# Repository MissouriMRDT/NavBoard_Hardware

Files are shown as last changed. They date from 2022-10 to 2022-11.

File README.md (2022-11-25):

# MRDT NavBoard Hardware
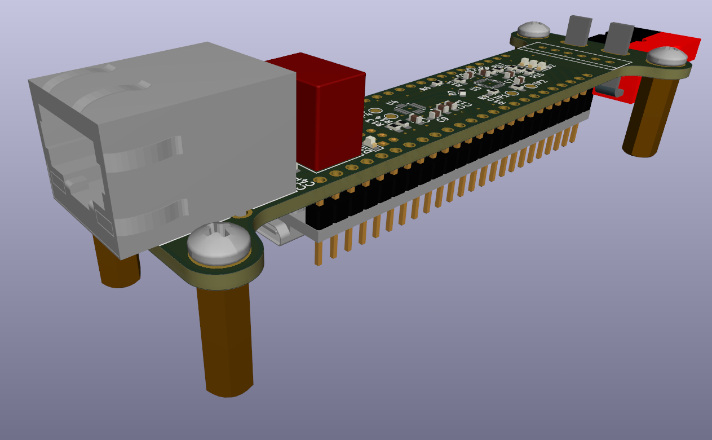
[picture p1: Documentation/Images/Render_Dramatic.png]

## Purpose
The Navigation (Nav) Board is responsible for containing, supplying, and interfacing the equipment required to determine the rover's position and orientation. This board does this by utilizing 2 inertial measurement units (IMUs) and a connection to an external GPS receiver. This data is processed and sent to the rest of the rover via an ethernet connection.
## Design
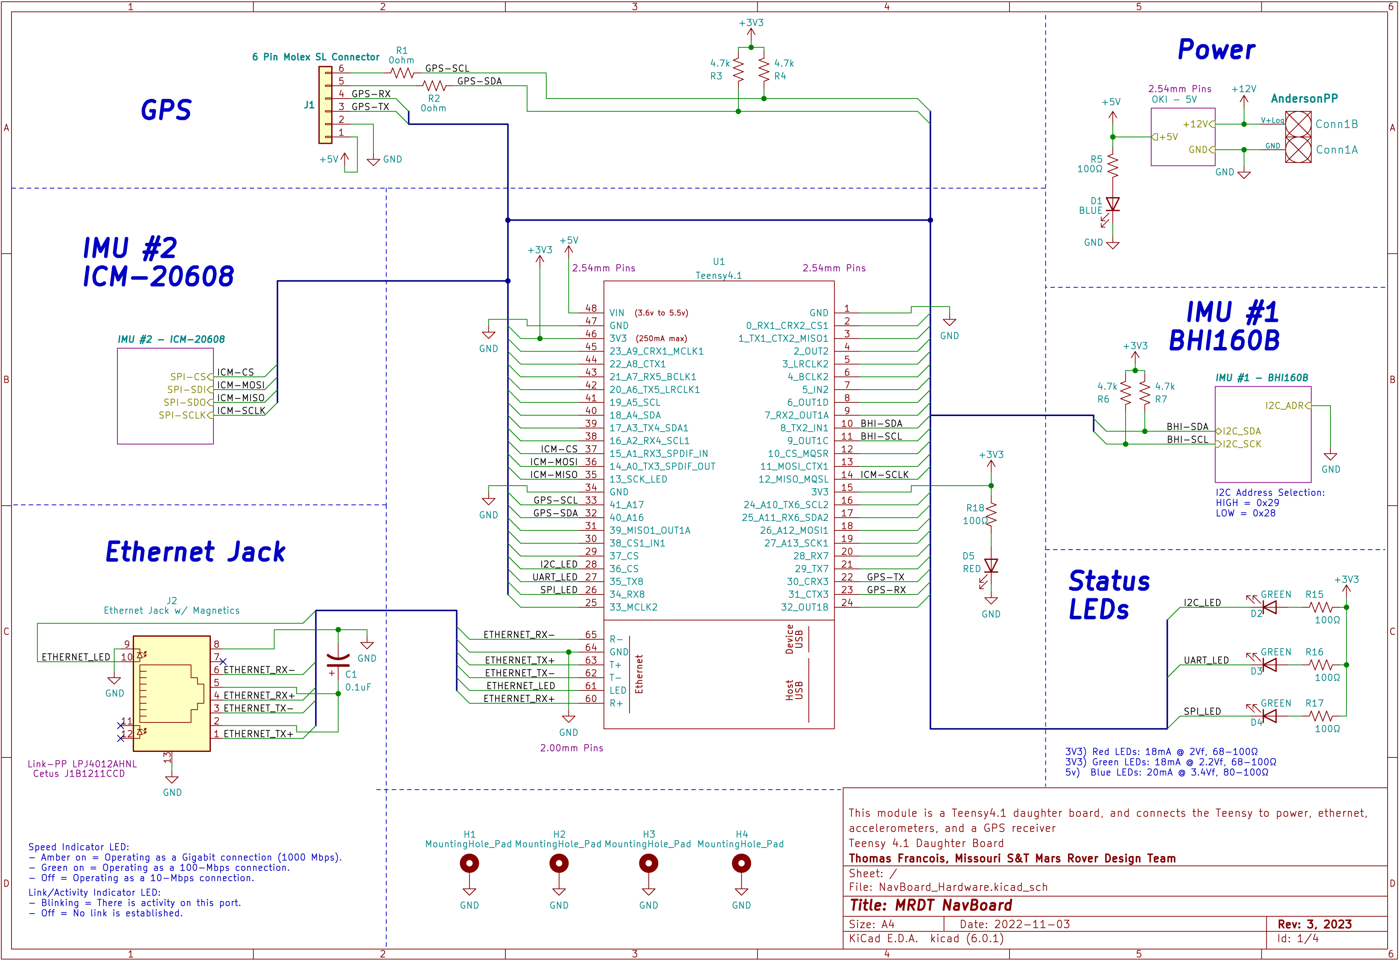
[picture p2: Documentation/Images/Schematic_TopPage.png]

This revision of the board is a new design, based on the components and connections from the 2022/2023 Rev 2 designs. The goal of this design was to make the board as small as possible, and to mount onto a Teensy 4.1 instead of a raspberry pi.

This design utilizes a 4-layer PCB with holes for M3 mounting screws on 15mm standoffs. The Teensy is soldered onto one side of the board, and all of the smd components are mounted on the other side.

This design also includes an ethernet RJ45 jack for allowing ethernet connectivity to the Teensy.

## Required External Connections
 - +12V
 - GPS (I2C and UART)
 - Teensy 4.1
 - Ethernet

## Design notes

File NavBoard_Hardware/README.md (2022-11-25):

# MRDT NavBoard PCB
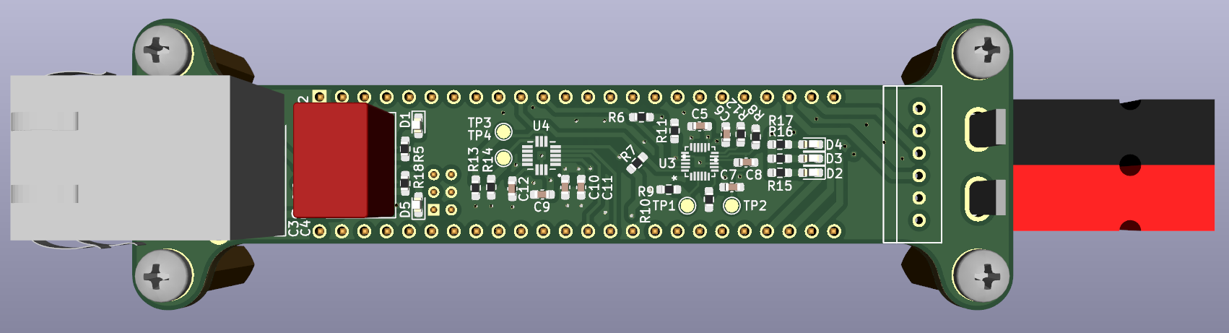
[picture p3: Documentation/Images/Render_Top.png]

## Dimensions
 - 100mm Long (124.29mm w/ Horizontal Power Poles)
 - 33.1mm Wide
## Board Specifications
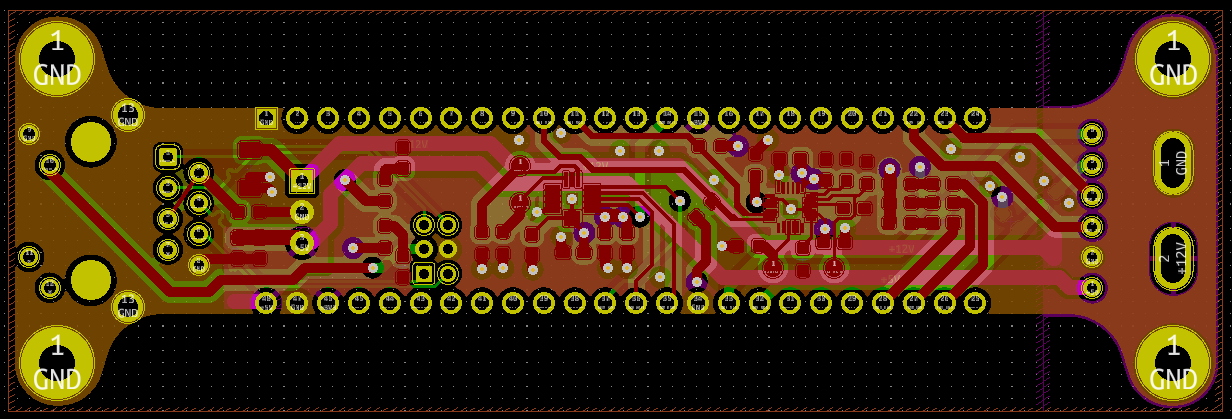
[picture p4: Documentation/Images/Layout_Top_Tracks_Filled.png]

 - 4-layer
  -- Top Copper (Signals, SMD Components, Ground Pour)
  -- Ground Copper
  -- Power Copper (3V3, 5V, 12V)
  -- Bottom Copper (Signals, Ethernet, Ground Pour)
 - 1-oz Copper
 - 1.6mm Thick
## Mounting Points
This module is designed as a daughter board to be mounted on top of a Teensy 4.1 microcontroller. There are holes at each corner of the board for mounting M3 standoffs. These holes are electrically connected to ground.

The powerpole connectors can be mounted vertically to reduce horizontal space.

The Teensy 4.1 needs to be mounted with the USB port facing the Ethernet port.

The Teensy 4.1 also needs to be mounted so that its reset button is accessible.

The MicroSD card should be accessible if the PowerPole connectors do not extend below the holes too much.

The Teensy 4.1 ethernet pins are 2.00mm pitch, NOT the standard 2.54mm. These also will likely need to be longer than standard 2.00mm pins, as 2.00 pins are shorter in length an 2.54mm pins.

The Teensy 4.1 CAN be socketed onto the PCB, but it is recommended for structural integrity reasons that it be direcly soldered into place using 2.54mm and 2.00mm pins.

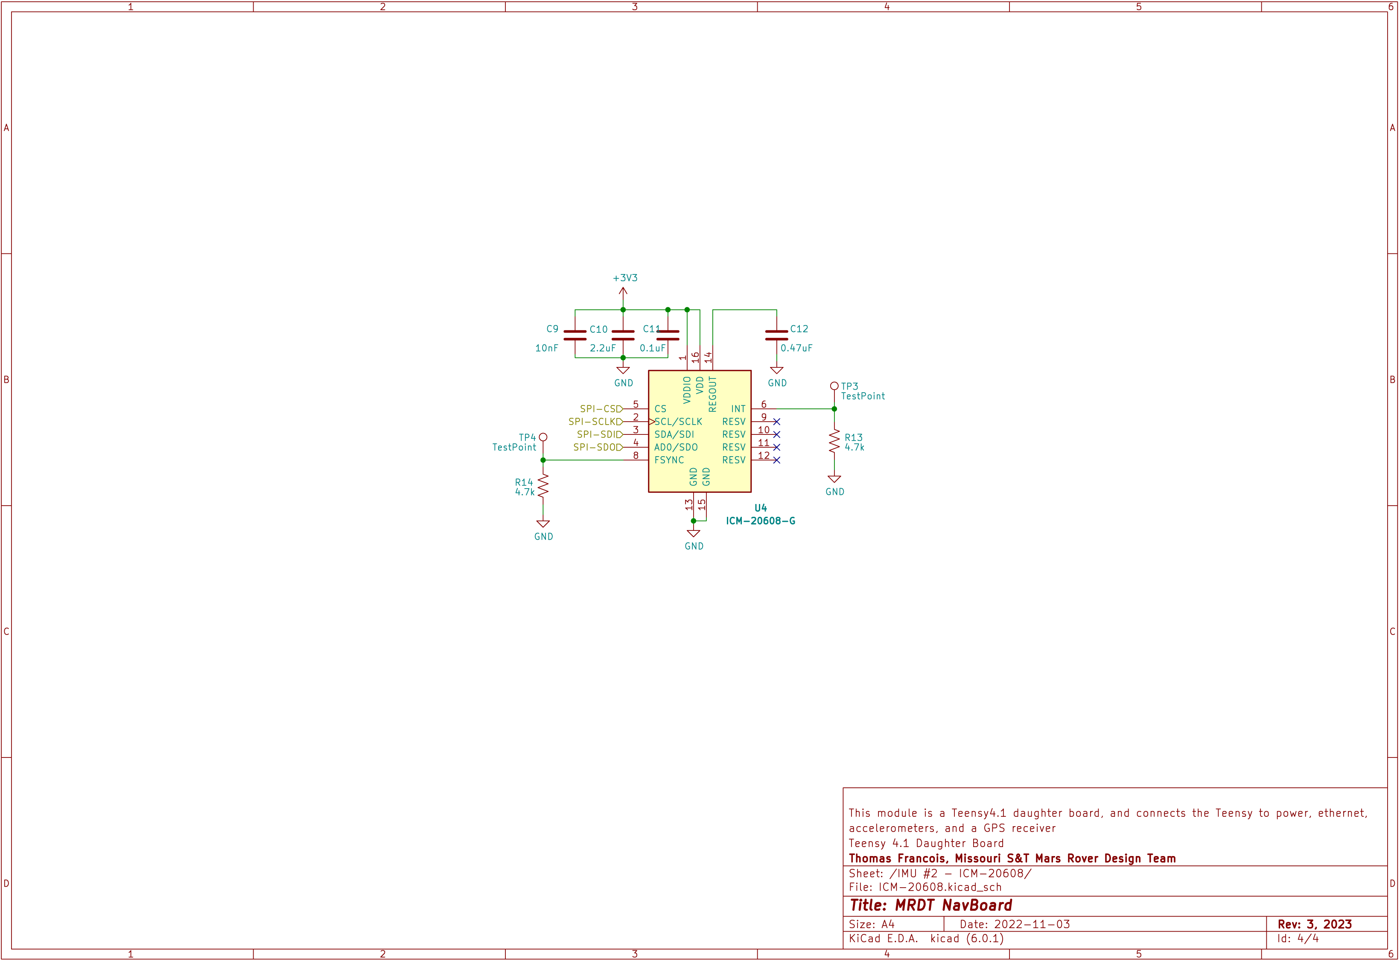
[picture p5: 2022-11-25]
Documentation/Images/Schematic_ICM-20608.png

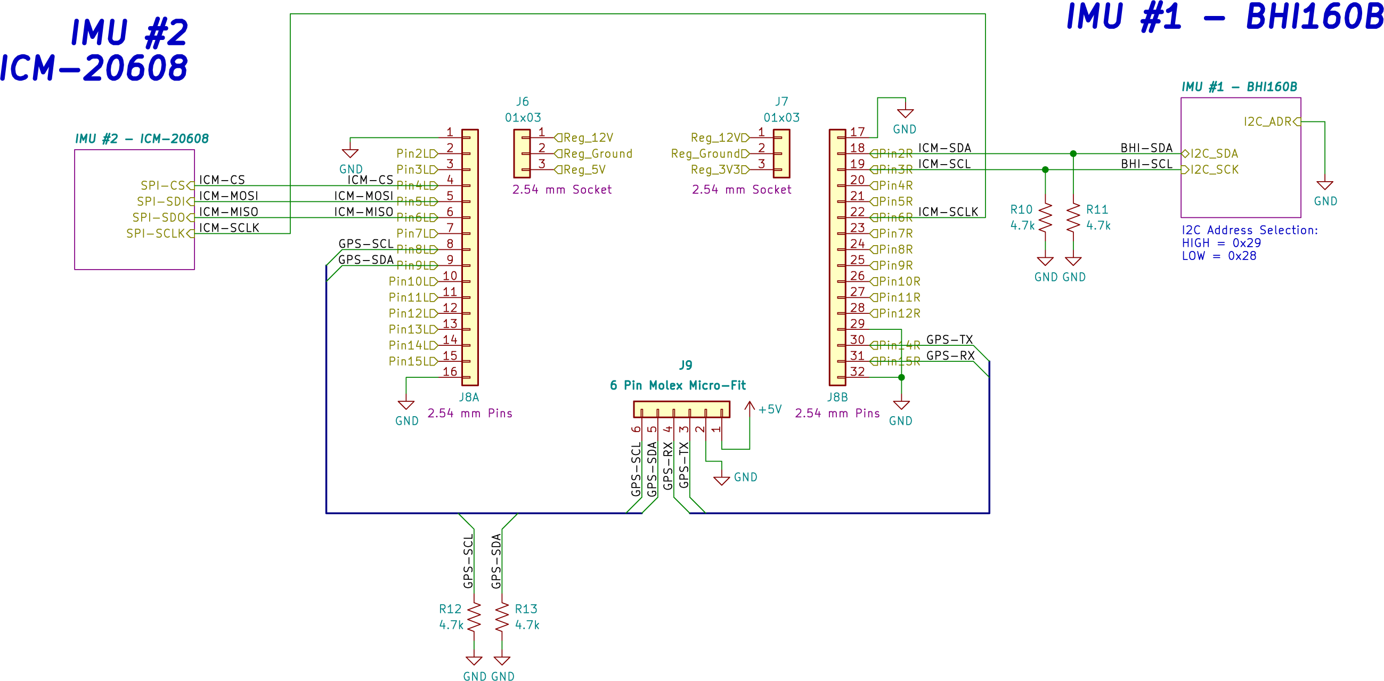
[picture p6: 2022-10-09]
Documentation/Schematic Screenshots/Top Board Sheet.png

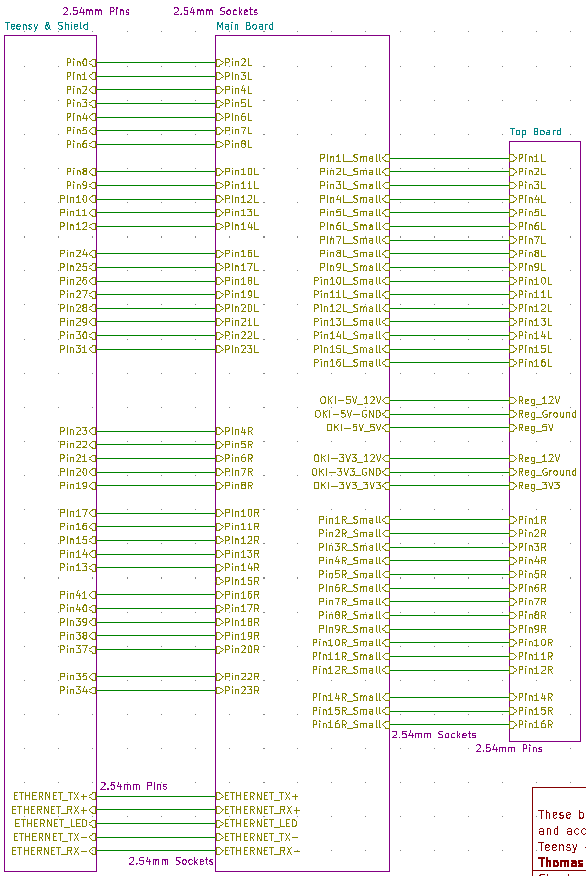
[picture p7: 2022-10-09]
Documentation/Schematic Screenshots/Screenshot 2022-10-09 160128.png

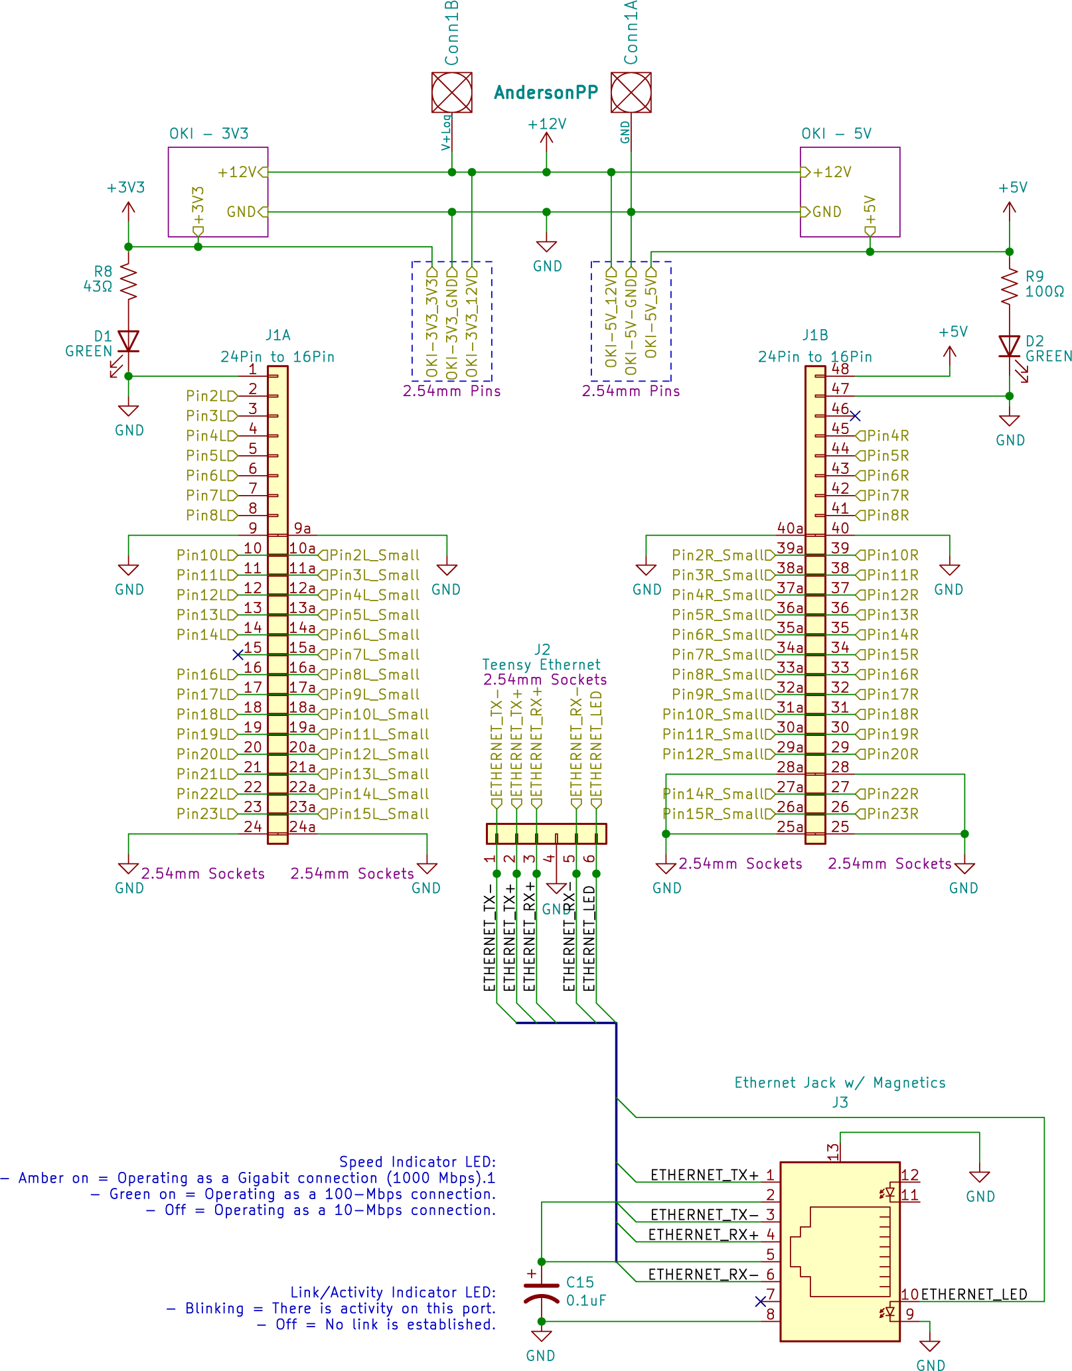
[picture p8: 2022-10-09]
Documentation/Schematic Screenshots/Main Board Sheet.png

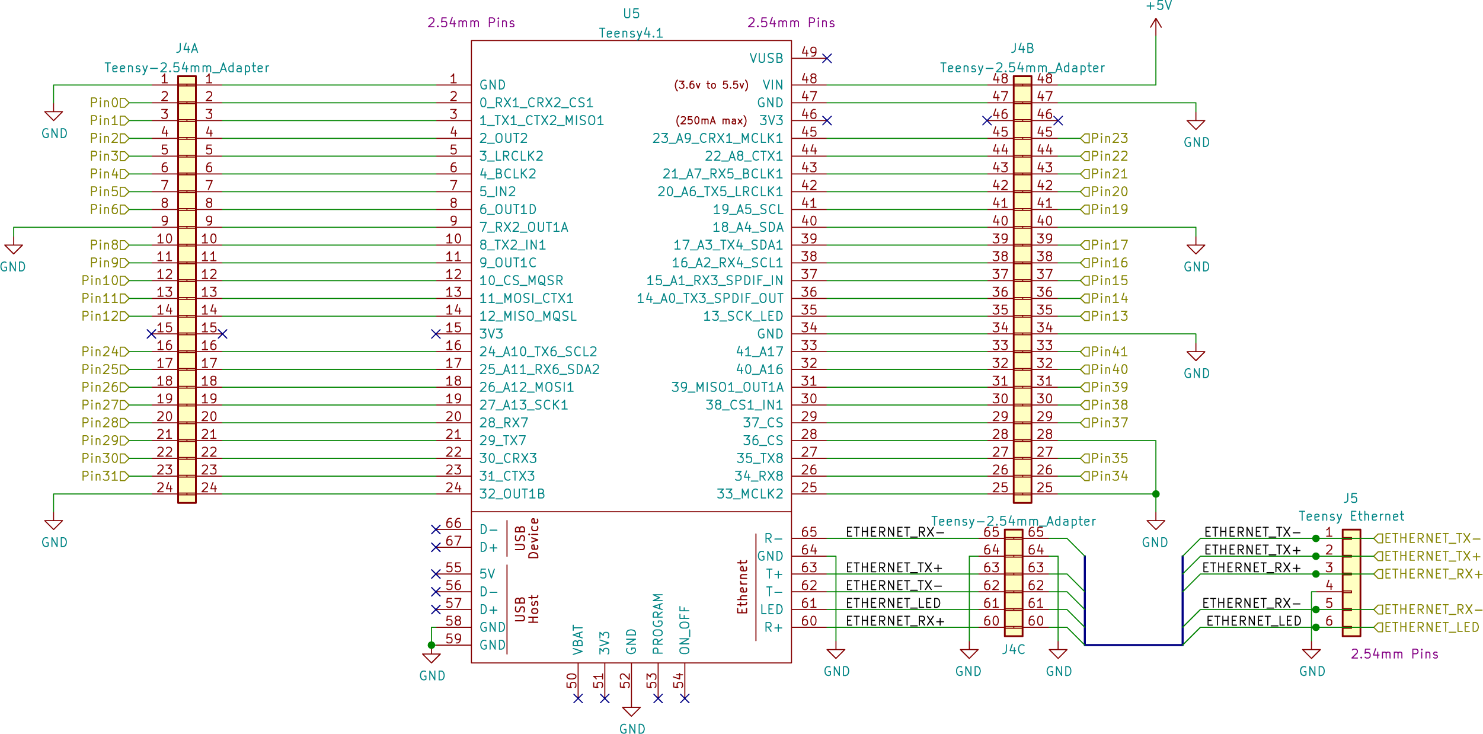
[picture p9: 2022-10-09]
Documentation/Schematic Screenshots/Teensy Shield Sheet.png

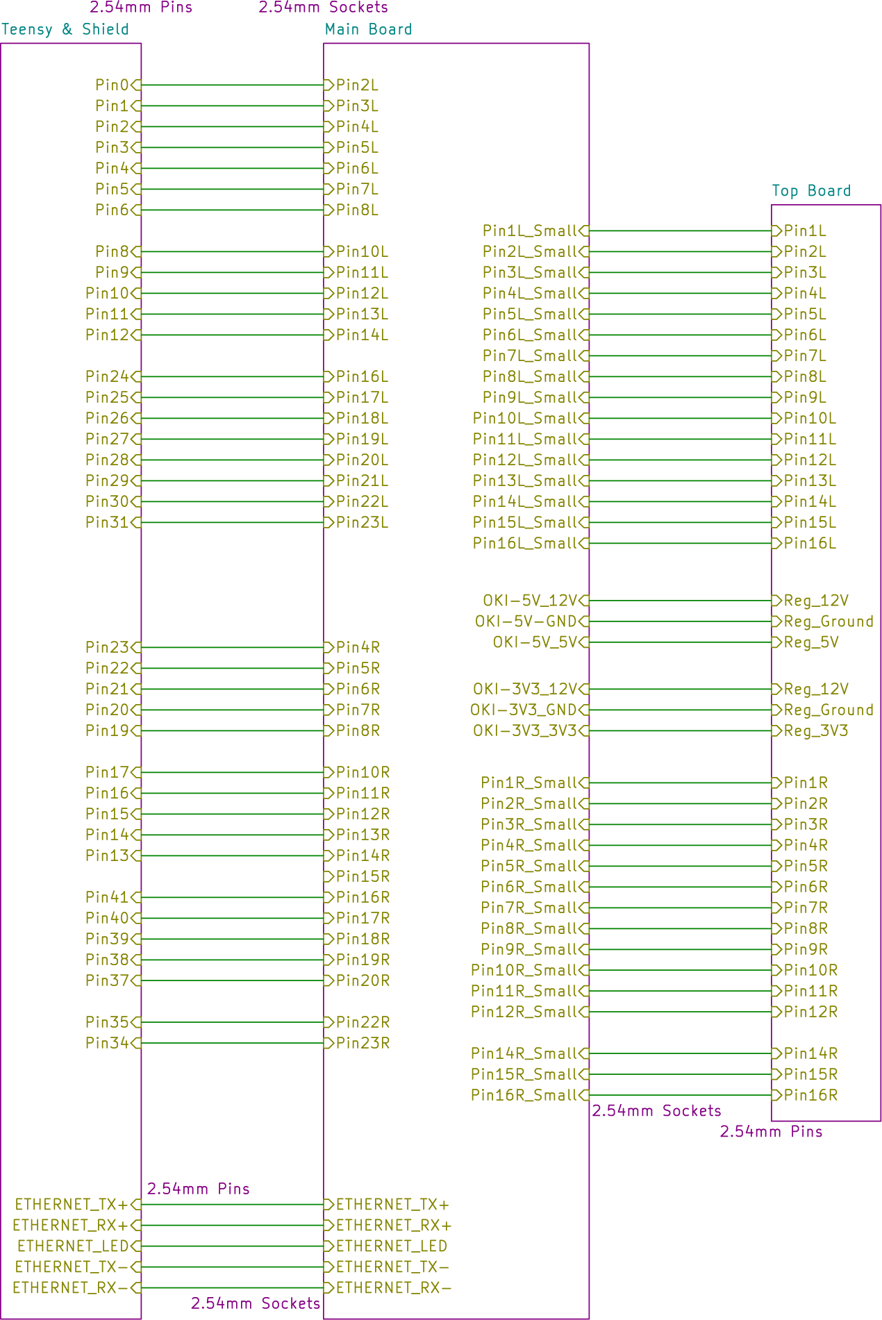
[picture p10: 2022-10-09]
Documentation/Schematic Screenshots/Main Overview Sheet.png

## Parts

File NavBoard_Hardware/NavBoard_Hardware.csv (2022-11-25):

Source: | C:\Users\frisc_000\Documents\GitHub\NavBoard_Hardware\NavBoard_Hardware\NavBoard_Hardware.kicad_sch
Date: | 11/4/2022 7:06:20 PM
Tool: | Eeschema (6.0.1)
Generator: | C:\Program Files\KiCad\6.0\bin\scripting\plugins/bom_csv_grouped_by_value.py
Component Count: | 50
Individual Components:
Item | Qty | Reference(s) | Value | LibPart | Footprint | Datasheet | Ethernet Headers | Left Headers | MANUFACTURER | PARTREV | Part Opt 1 | Part Opt 2 | Right Headers | STANDARD
 |  | C1 | 0.1uF | Device:C_Polarized_US | Capacitor_SMD:C_0603_1608Metric_Pad1.08x0.95mm_HandSolder | ~
 |  | C2 | 22uF 50V | Device:C_Polarized_US | Capacitor_SMD:C_1206_3216Metric_Pad1.33x1.80mm_HandSolder | ~
 |  | C3 | 10uF | Device:C_Polarized_US | Capacitor_SMD:C_0603_1608Metric_Pad1.08x0.95mm_HandSolder | ~
 |  | C4 | 0.1uF | Device:C_Polarized_US | Capacitor_SMD:C_0603_1608Metric_Pad1.08x0.95mm_HandSolder | ~
 |  | C5 | 0.1uF | Device:C | Capacitor_SMD:C_0603_1608Metric_Pad1.08x0.95mm_HandSolder | ~
 |  | C6 | 1uF | Device:C | Capacitor_SMD:C_0603_1608Metric_Pad1.08x0.95mm_HandSolder | ~
 |  | C7 | 0.1uF | Device:C | Capacitor_SMD:C_0603_1608Metric_Pad1.08x0.95mm_HandSolder | ~
 |  | C8 | 0.47uF | Device:C | Capacitor_SMD:C_0603_1608Metric_Pad1.08x0.95mm_HandSolder | ~
 |  | C9 | 10nF | Device:C | Capacitor_SMD:C_0603_1608Metric_Pad1.08x0.95mm_HandSolder | ~
 |  | C10 | 2.2uF | Device:C | Capacitor_SMD:C_0603_1608Metric_Pad1.08x0.95mm_HandSolder | ~
 |  | C11 | 0.1uF | Device:C | Capacitor_SMD:C_0603_1608Metric_Pad1.08x0.95mm_HandSolder | ~
 |  | C12 | 0.47uF | Device:C | Capacitor_SMD:C_0603_1608Metric_Pad1.08x0.95mm_HandSolder | ~
 |  | Conn1 | AndersonPP | MRDT_Connectors:AndersonPP | MRDT_Connectors:Square_Anderson_2_H_Side_By_Side
 |  | D1 | BLUE | Device:LED | LED_SMD:LED_0603_1608Metric_Pad1.05x0.95mm_HandSolder | ~
 |  | D2 | GREEN | Device:LED | LED_SMD:LED_0603_1608Metric_Pad1.05x0.95mm_HandSolder | ~
 |  | D3 | GREEN | Device:LED | LED_SMD:LED_0603_1608Metric_Pad1.05x0.95mm_HandSolder | ~
 |  | D4 | GREEN | Device:LED | LED_SMD:LED_0603_1608Metric_Pad1.05x0.95mm_HandSolder | ~
 |  | D5 | RED | Device:LED | LED_SMD:LED_0603_1608Metric_Pad1.05x0.95mm_HandSolder | ~
 |  | H1 | MountingHole_Pad | Mechanical:MountingHole_Pad |  | ~
 |  | H2 | MountingHole_Pad | Mechanical:MountingHole_Pad |  | ~
 |  | H3 | MountingHole_Pad | Mechanical:MountingHole_Pad |  | ~
 |  | H4 | MountingHole_Pad | Mechanical:MountingHole_Pad |  | ~
 |  | J1 | 6 Pin Molex SL Connector | Connector_Generic:Conn_01x06 | Nav_Board:MOLEX_SL_06_Vertical | ~
 |  | J2 | Ethernet Jack w/ Magnetics | Connector:8P8C_LED_Shielded | Connector_RJ:RJ45_Cetus_J1B1211CCD_Horizontal | https://www.pjrc.com/store/j1b1211ccd.pdf |  |  |  |  | Link-PP LPJ4012AHNL | Cetus J1B1211CCD
 |  | R1 | 0ohm | Device:R_US | Resistor_SMD:R_0603_1608Metric_Pad0.98x0.95mm_HandSolder | ~
 |  | R2 | 0ohm | Device:R_US | Resistor_SMD:R_0603_1608Metric_Pad0.98x0.95mm_HandSolder | ~
 |  | R3 | 4.7k | Device:R_US | Resistor_SMD:R_0603_1608Metric_Pad0.98x0.95mm_HandSolder | ~
 |  | R4 | 4.7k | Device:R_US | Resistor_SMD:R_0603_1608Metric_Pad0.98x0.95mm_HandSolder | ~
 |  | R5 | 100Ω | Device:R_US | Resistor_SMD:R_0603_1608Metric_Pad0.98x0.95mm_HandSolder | ~
 |  | R6 | 4.7k | Device:R_US | Resistor_SMD:R_0603_1608Metric_Pad0.98x0.95mm_HandSolder | ~
 |  | R7 | 4.7k | Device:R_US | Resistor_SMD:R_0603_1608Metric_Pad0.98x0.95mm_HandSolder | ~
 |  | R8 | 4.7k | Device:R_US | Resistor_SMD:R_0603_1608Metric_Pad0.98x0.95mm_HandSolder | ~
 |  | R9 | 4.7k | Device:R_US | Resistor_SMD:R_0603_1608Metric_Pad0.98x0.95mm_HandSolder | ~
 |  | R10 | 4.7k | Device:R_US | Resistor_SMD:R_0603_1608Metric_Pad0.98x0.95mm_HandSolder | ~
 |  | R11 | 4.7k | Device:R_US | Resistor_SMD:R_0603_1608Metric_Pad0.98x0.95mm_HandSolder | ~
 |  | R12 | 4.7k | Device:R_US | Resistor_SMD:R_0603_1608Metric_Pad0.98x0.95mm_HandSolder | ~
 |  | R13 | 4.7k | Device:R_US | Resistor_SMD:R_0603_1608Metric_Pad0.98x0.95mm_HandSolder | ~
 |  | R14 | 4.7k | Device:R_US | Resistor_SMD:R_0603_1608Metric_Pad0.98x0.95mm_HandSolder | ~
 |  | R15 | 100Ω | Device:R_US | Resistor_SMD:R_0603_1608Metric_Pad0.98x0.95mm_HandSolder | ~
 |  | R16 | 100Ω | Device:R_US | Resistor_SMD:R_0603_1608Metric_Pad0.98x0.95mm_HandSolder | ~
 |  | R17 | 100Ω | Device:R_US | Resistor_SMD:R_0603_1608Metric_Pad0.98x0.95mm_HandSolder | ~
 |  | R18 | 100Ω | Device:R_US | Resistor_SMD:R_0603_1608Metric_Pad0.98x0.95mm_HandSolder | ~
 |  | TP1 | TestPoint | Connector:TestPoint | TestPoint:TestPoint_Pad_D1.5mm | ~
 |  | TP2 | TestPoint | Connector:TestPoint | TestPoint:TestPoint_Pad_D1.5mm | ~
 |  | TP3 | TestPoint | Connector:TestPoint | TestPoint:TestPoint_Pad_D1.5mm | ~
 |  | TP4 | TestPoint | Connector:TestPoint | TestPoint:TestPoint_Pad_D1.5mm | ~
 |  | U1 | Teensy4.1 | teensy:Teensy4.1 | Nav_Board:Teensy41 | https://www.pjrc.com/store/teensy41.html | 2.00mm Pins | 2.54mm Pins |  |  |  |  | 2.54mm Pins
 |  | U2 | OKI-5V | MRDT_Devices:OKI | Nav_Board:OKI_Vertical_TSR
 |  | U3 | BHI160B | MRDT_Sensors:BHI160B | Nav_Board:BHI160B_ExtendedPads | https://www.bosch-sensortec.com/media/boschsensortec/downloads/datasheets/bst-bhi160b-ds000.pdf
 |  | U4 | ICM-20608-G | MRDT_Sensors:ICM-20608-G | Nav_Board:ICM-20608-G_ExtendedPads | https://invensense.tdk.com/wp-content/uploads/2015/03/DS-000081-v1.01.pdf |  |  | TDK | 1.0 |  |  |  | IPC-7351B
Collated Components:
Item | Qty | Reference(s) | Value | LibPart | Footprint | Datasheet | Ethernet Headers | Left Headers | MANUFACTURER | PARTREV | Part Opt 1 | Part Opt 2 | Right Headers | STANDARD
1 | 2 | C1, C4 | 0.1uF | Device:C_Polarized_US | Capacitor_SMD:C_0603_1608Metric_Pad1.08x0.95mm_HandSolder | ~
2 | 1 | C2 | 22uF 50V | Device:C_Polarized_US | Capacitor_SMD:C_1206_3216Metric_Pad1.33x1.80mm_HandSolder | ~
3 | 1 | C3 | 10uF | Device:C_Polarized_US | Capacitor_SMD:C_0603_1608Metric_Pad1.08x0.95mm_HandSolder | ~
4 | 3 | C5, C7, C11 | 0.1uF | Device:C | Capacitor_SMD:C_0603_1608Metric_Pad1.08x0.95mm_HandSolder | ~
5 | 1 | C6 | 1uF | Device:C | Capacitor_SMD:C_0603_1608Metric_Pad1.08x0.95mm_HandSolder | ~
6 | 2 | C8, C12 | 0.47uF | Device:C | Capacitor_SMD:C_0603_1608Metric_Pad1.08x0.95mm_HandSolder | ~
7 | 1 | C9 | 10nF | Device:C | Capacitor_SMD:C_0603_1608Metric_Pad1.08x0.95mm_HandSolder | ~
8 | 1 | C10 | 2.2uF | Device:C | Capacitor_SMD:C_0603_1608Metric_Pad1.08x0.95mm_HandSolder | ~
9 | 1 | Conn1 | AndersonPP | MRDT_Connectors:AndersonPP | MRDT_Connectors:Square_Anderson_2_H_Side_By_Side
10 | 1 | D1 | BLUE | Device:LED | LED_SMD:LED_0603_1608Metric_Pad1.05x0.95mm_HandSolder | ~
11 | 3 | D2, D3, D4 | GREEN | Device:LED | LED_SMD:LED_0603_1608Metric_Pad1.05x0.95mm_HandSolder | ~
12 | 1 | D5 | RED | Device:LED | LED_SMD:LED_0603_1608Metric_Pad1.05x0.95mm_HandSolder | ~
13 | 4 | H1, H2, H3, H4 | MountingHole_Pad | Mechanical:MountingHole_Pad |  | ~
14 | 1 | J1 | 6 Pin Molex SL Connector | Connector_Generic:Conn_01x06 | Nav_Board:MOLEX_SL_06_Vertical | ~
15 | 1 | J2 | Ethernet Jack w/ Magnetics | Connector:8P8C_LED_Shielded | Connector_RJ:RJ45_Cetus_J1B1211CCD_Horizontal | https://www.pjrc.com/store/j1b1211ccd.pdf |  |  |  |  | Link-PP LPJ4012AHNL | Cetus J1B1211CCD
16 | 2 | R1, R2 | 0ohm | Device:R_US | Resistor_SMD:R_0603_1608Metric_Pad0.98x0.95mm_HandSolder | ~
17 | 11 | R3, R4, R6, R7, R8, R9, R10, R11, R12, R13, R14 | 4.7k | Device:R_US | Resistor_SMD:R_0603_1608Metric_Pad0.98x0.95mm_HandSolder | ~
18 | 5 | R5, R15, R16, R17, R18 | 100Ω | Device:R_US | Resistor_SMD:R_0603_1608Metric_Pad0.98x0.95mm_HandSolder | ~
19 | 4 | TP1, TP2, TP3, TP4 | TestPoint | Connector:TestPoint | TestPoint:TestPoint_Pad_D1.5mm | ~
20 | 1 | U1 | Teensy4.1 | teensy:Teensy4.1 | Nav_Board:Teensy41 | https://www.pjrc.com/store/teensy41.html | 2.00mm Pins | 2.54mm Pins |  |  |  |  | 2.54mm Pins
21 | 1 | U2 | OKI-5V | MRDT_Devices:OKI | Nav_Board:OKI_Vertical_TSR
22 | 1 | U3 | BHI160B | MRDT_Sensors:BHI160B | Nav_Board:BHI160B_ExtendedPads | https://www.bosch-sensortec.com/media/boschsensortec/downloads/datasheets/bst-bhi160b-ds000.pdf
23 | 1 | U4 | ICM-20608-G | MRDT_Sensors:ICM-20608-G | Nav_Board:ICM-20608-G_ExtendedPads | https://invensense.tdk.com/wp-content/uploads/2015/03/DS-000081-v1.01.pdf |  |  | TDK | 1.0 |  |  |  | IPC-7351B

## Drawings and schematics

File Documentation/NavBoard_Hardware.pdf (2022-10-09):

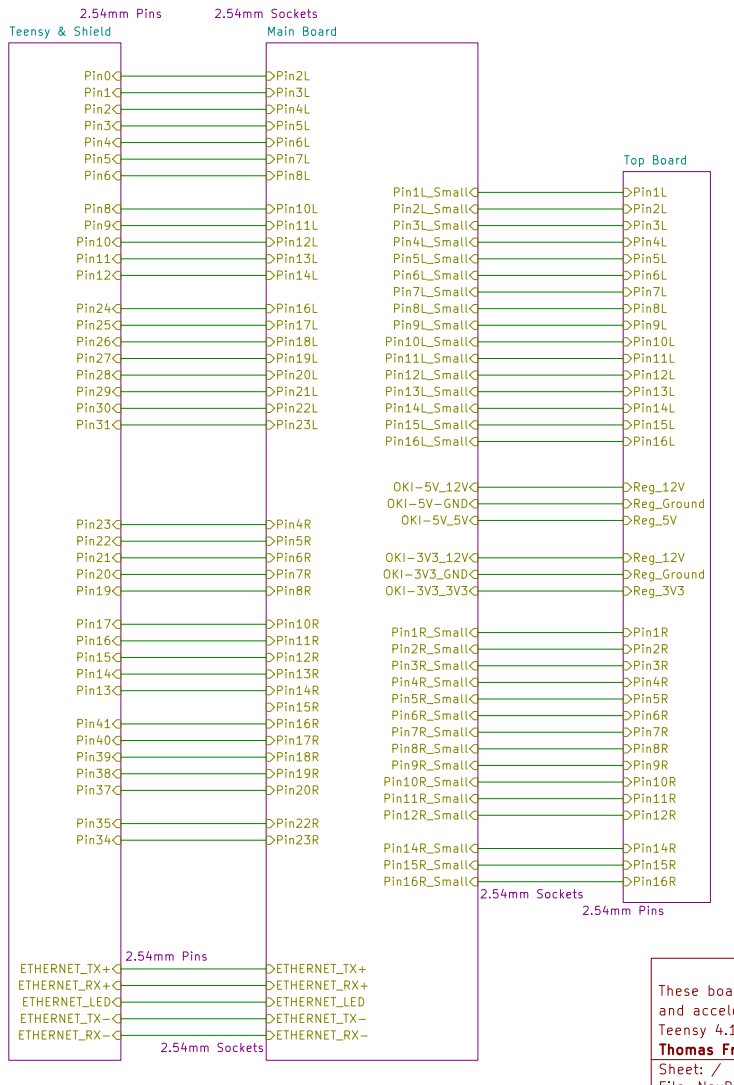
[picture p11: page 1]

Teensy 4.1 Daughter Boards and Modules and accelerometers These boards are to be stacked together, and connects the Teensy to power, ethernet, Pin14R
Pin15R
Pin16R

File: NavBoard_Hardware.kicad_sch Sheet: / Thomas Francois, Missouri S&T Mars Rover Design Team

Id: 1/8 Title: MRDT NavBoard

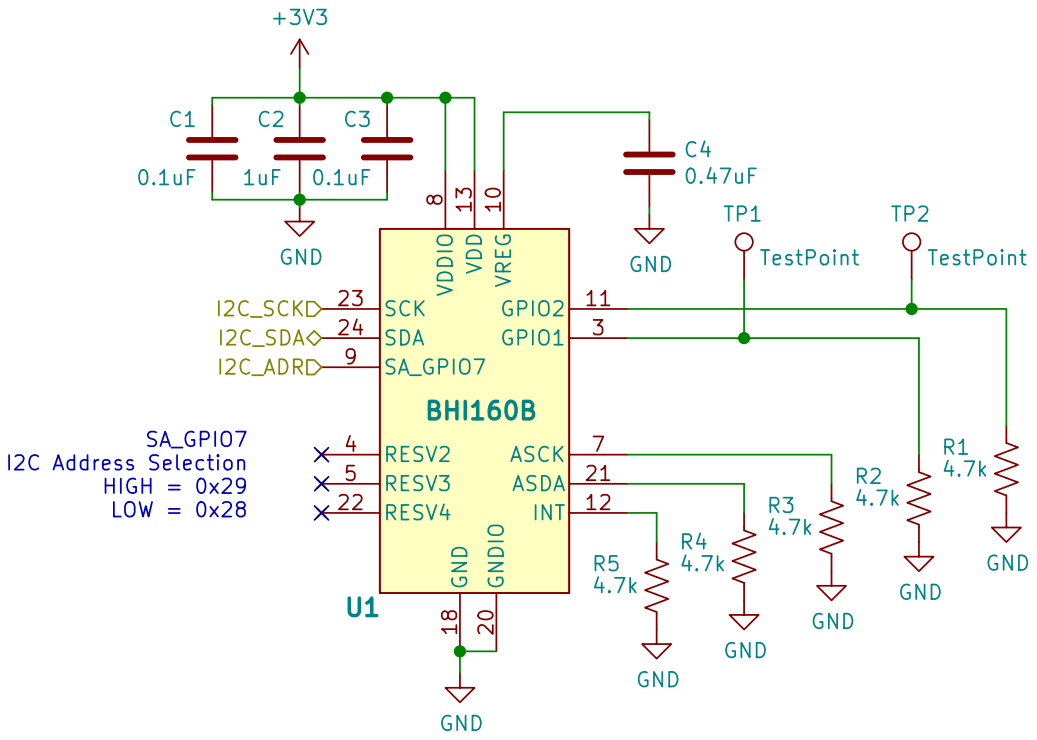
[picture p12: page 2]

BHI160B Inertial Measurement Unit & Supporting Components Provides Position and Acceleration Data R3

Thomas Francois, Missouri S&T Mars Rover Design Team
Sheet: /Top Board/IMU #1 - BHI160B/
File: BHI160B.kicad_sch
Id: 2/8 Title: MRDT NavBoard - BHI160B

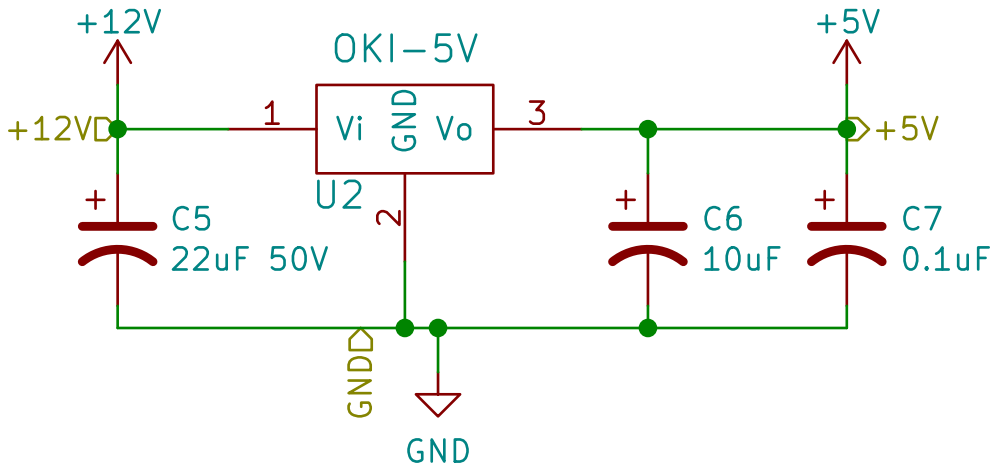
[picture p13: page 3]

Provides stable 5V from 12V input GND

OKI 5V Voltage Regulator
File: OKI-5V.kicad_sch Sheet: /Main Board/OKI - 5V/ Thomas Francois, Missouri S&T Mars Rover Design Team

Id: 3/8 Title: MRDT NavBoard

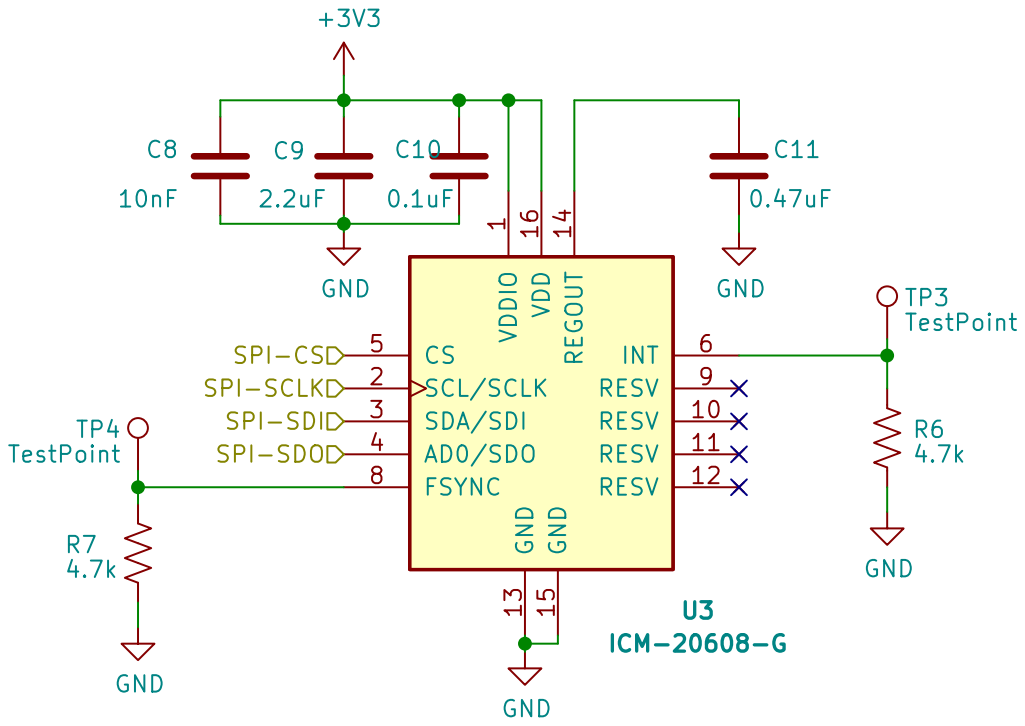
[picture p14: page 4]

1 RESV 10 RESV 11 RESV 12 GND 13 REGOUT 14 GND 15 VDD 16 SCL/SCLK 2 SDA/SDI 3 AD0/SDO 4 CS 5

SPI-CS
SPI-SDI SPI-SCLK

Inertial Measurement Unit and Supporting Components Provides Position & Acceleration Data

Thomas Francois, Missouri S&T Mars Rover Design Team
Sheet: /Top Board/IMU #2 - ICM-20608/
File: ICM-20608.kicad_sch
Id: 4/8 Title: MRDT NavBoard - ICM-20608-G

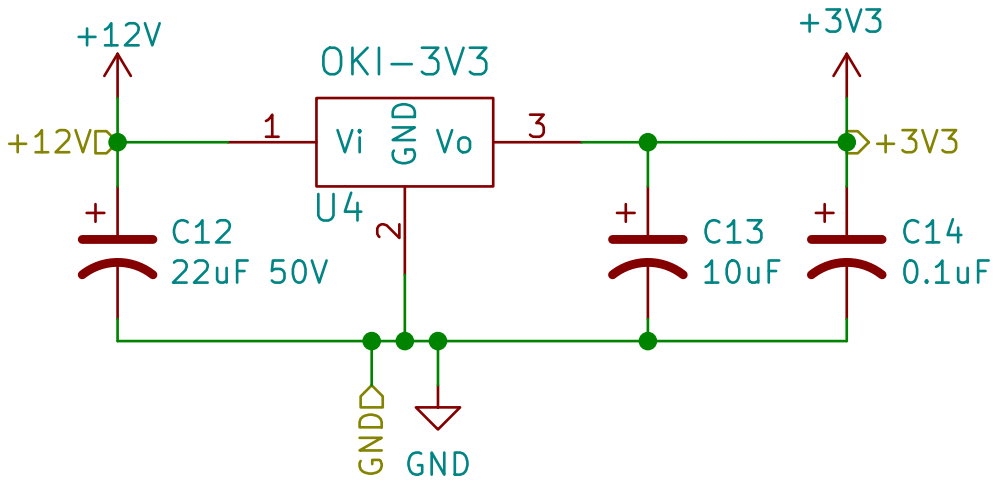
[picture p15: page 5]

Provides stable 3V3 from 12V input C12

OKI 3V3 Voltage Regulator
File: OKI-3V3.kicad_sch Sheet: /Main Board/OKI - 3V3/ Thomas Francois, Missouri S&T Mars Rover Design Team

Id: 5/8 Title: MRDT NavBoard - OKI 3V3 Voltage Regulator

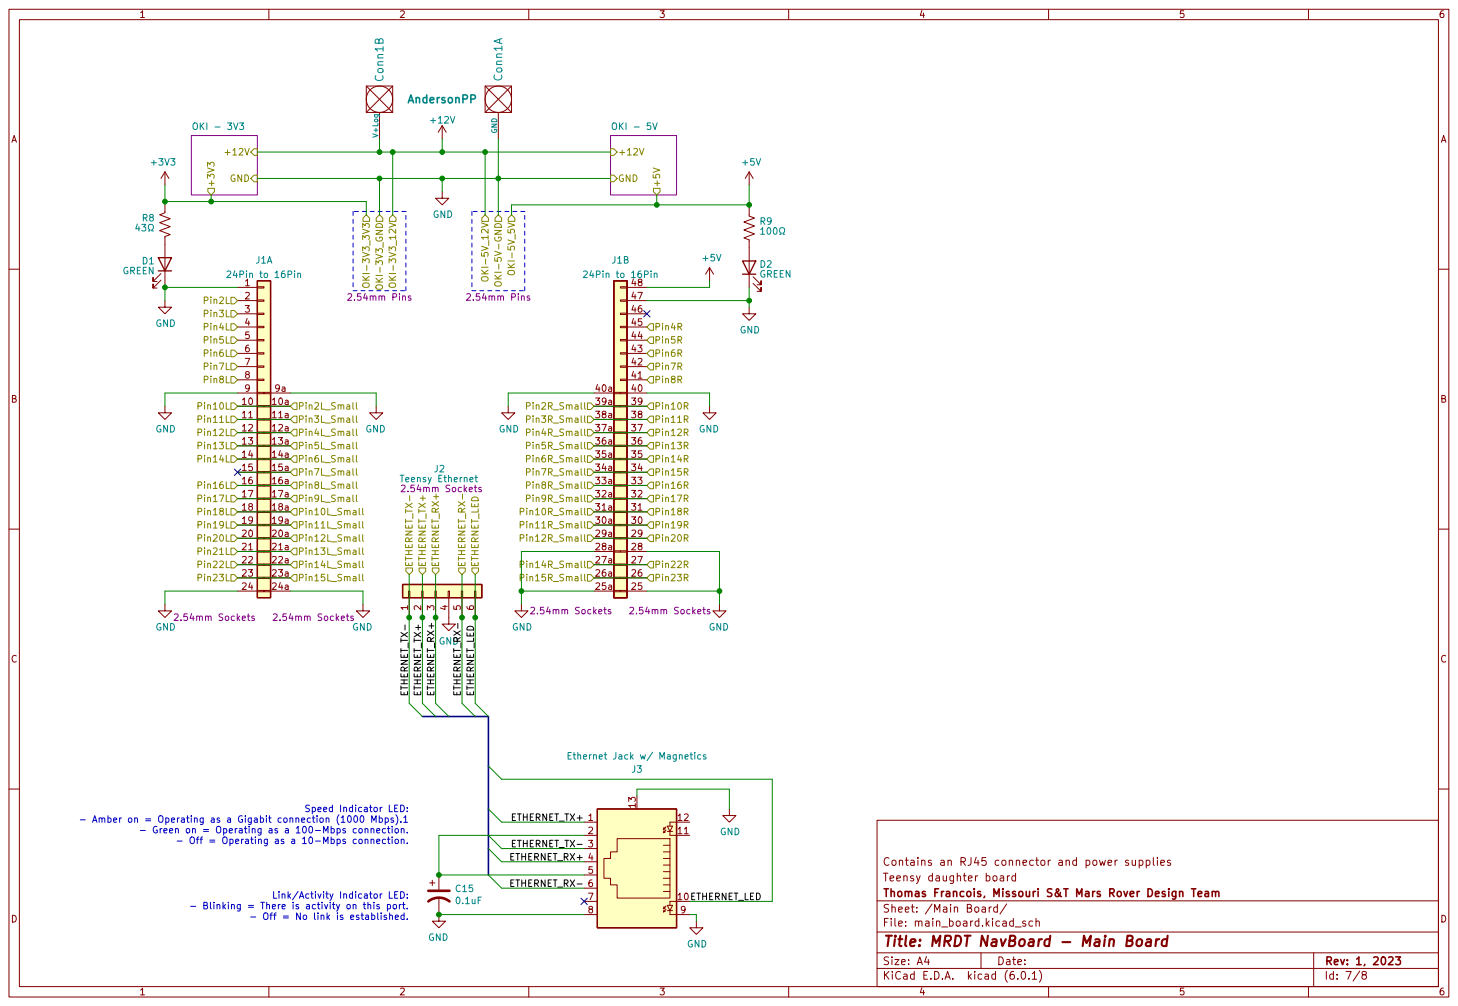
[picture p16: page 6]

- Amber on = Operating as a Gigabit connection (1000 Mbps).1

- Green on = Operating as a 100-Mbps connection.
- Off = Operating as a 10-Mbps connection.

Contains an RJ45 connector and power supplies
Teensy daughter board
File: main_board.kicad_sch Sheet: /Main Board/ Thomas Francois, Missouri S&T Mars Rover Design Team

- Blinking = There is activity on this port. - Off = No link is established.

Link/Activity Indicator LED:

Id: 7/8 Title: MRDT NavBoard - Main Board

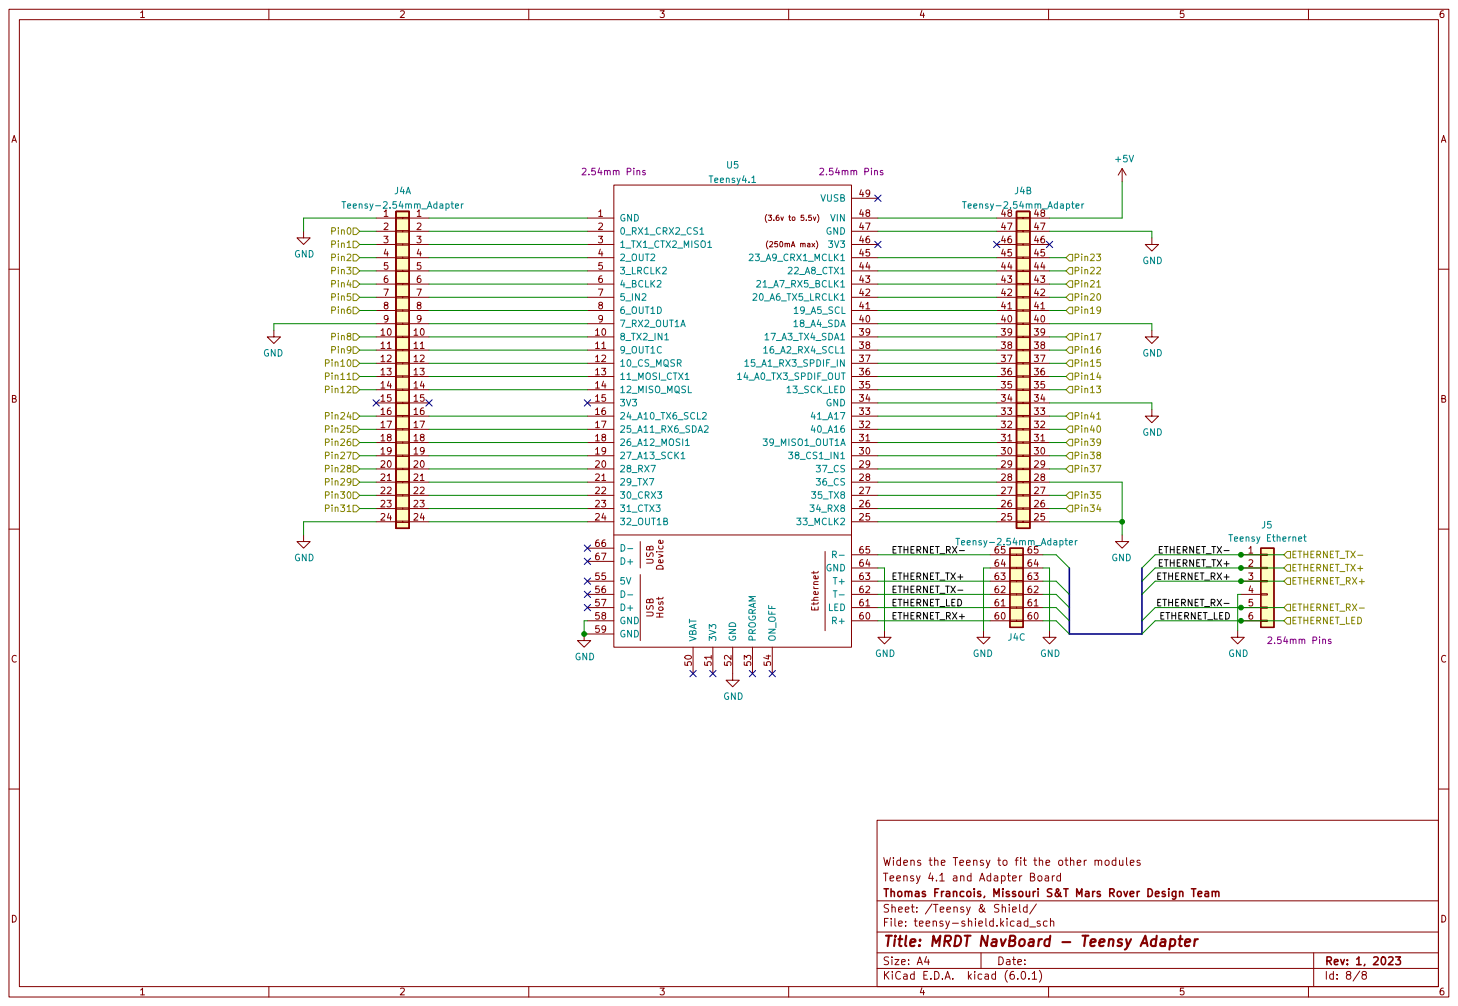
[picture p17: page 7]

30_CRX3 22 | 27 | 27
31_CTX3 23 | 26 | 26

Widens the Teensy to fit the other modules GND

Teensy 4.1 and Adapter Board
Thomas Francois, Missouri S&T Mars Rover Design Team
Sheet: /Teensy & Shield/
File: teensy-shield.kicad_sch
Id: 8/8 Title: MRDT NavBoard - Teensy Adapter

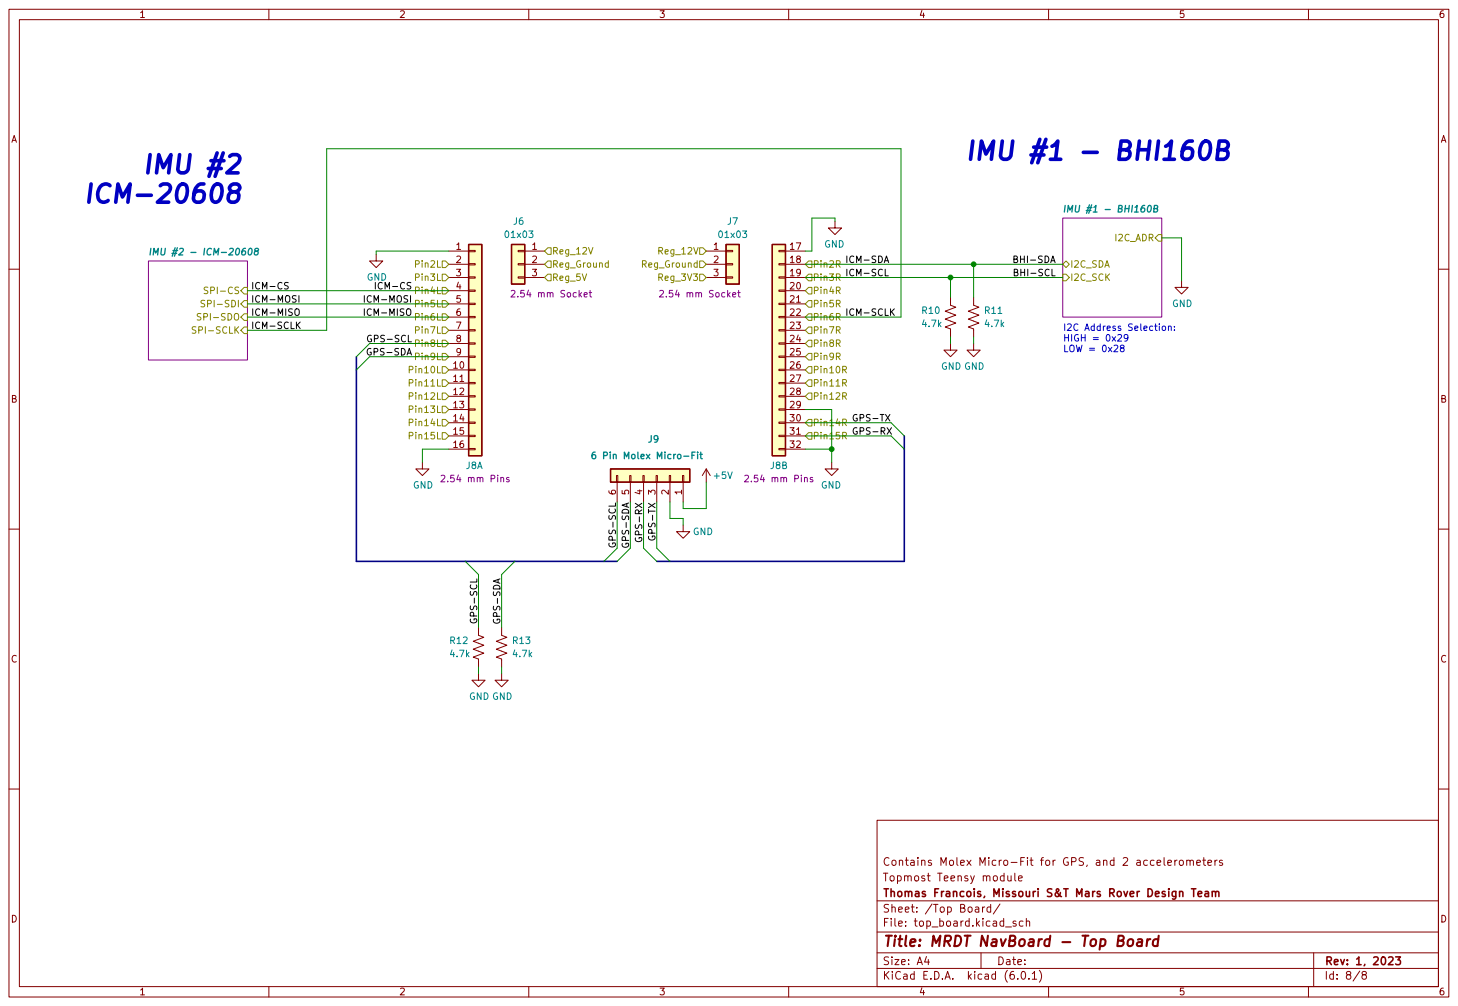
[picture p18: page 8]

BHI-SCL GPS-SCL GPS-SDA
ICM-CS

ICM-SCL GPS-SDA

SPI-CS
SPI-SDI SPI-SDO

20 Pin4R 21 22 ICM-SCLK

ICM-MOSI | 5
ICM-MISO | ICM-MISO 6
ICM-SCLK

Contains Molex Micro-Fit for GPS, and 2 accelerometers
Topmost Teensy module
Thomas Francois, Missouri S&T Mars Rover Design Team
Sheet: /Top Board/
File: top_board.kicad_sch
Id: 8/8 Title: MRDT NavBoard - Top Board

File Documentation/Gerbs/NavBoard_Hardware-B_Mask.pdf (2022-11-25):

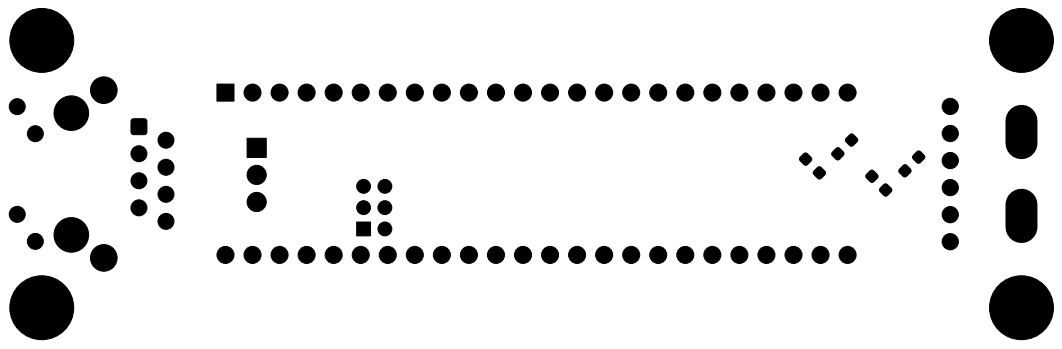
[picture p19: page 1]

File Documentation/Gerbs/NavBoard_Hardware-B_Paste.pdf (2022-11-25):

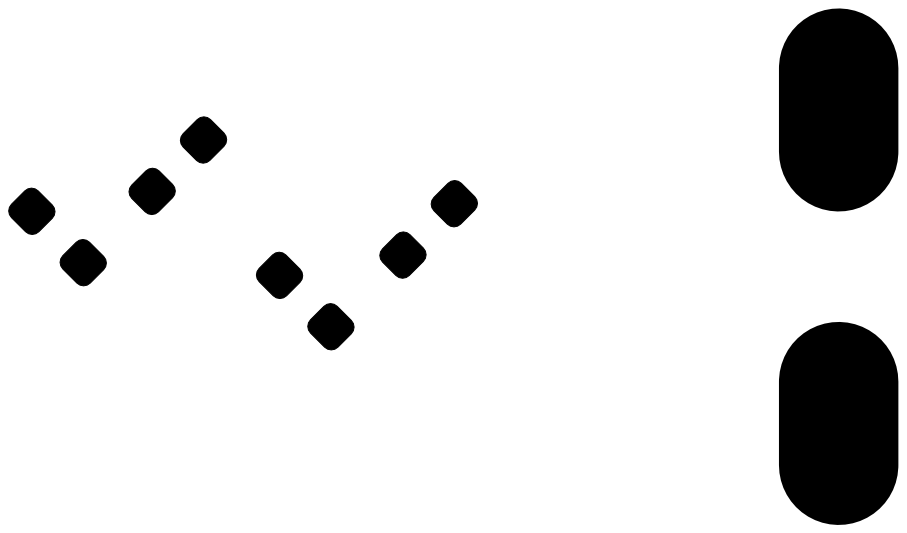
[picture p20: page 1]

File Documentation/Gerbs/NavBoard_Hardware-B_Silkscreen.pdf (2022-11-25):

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

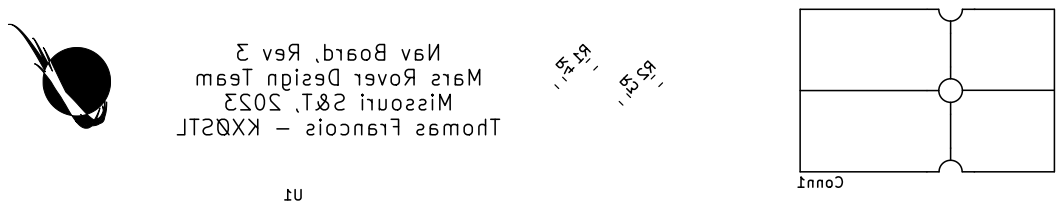
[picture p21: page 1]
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

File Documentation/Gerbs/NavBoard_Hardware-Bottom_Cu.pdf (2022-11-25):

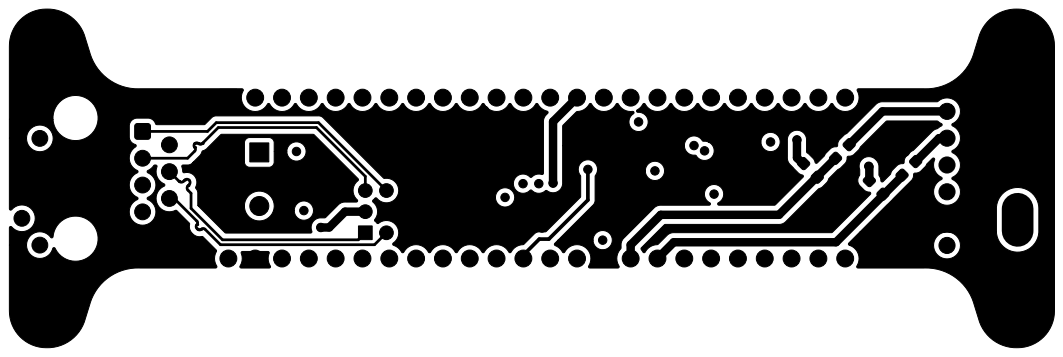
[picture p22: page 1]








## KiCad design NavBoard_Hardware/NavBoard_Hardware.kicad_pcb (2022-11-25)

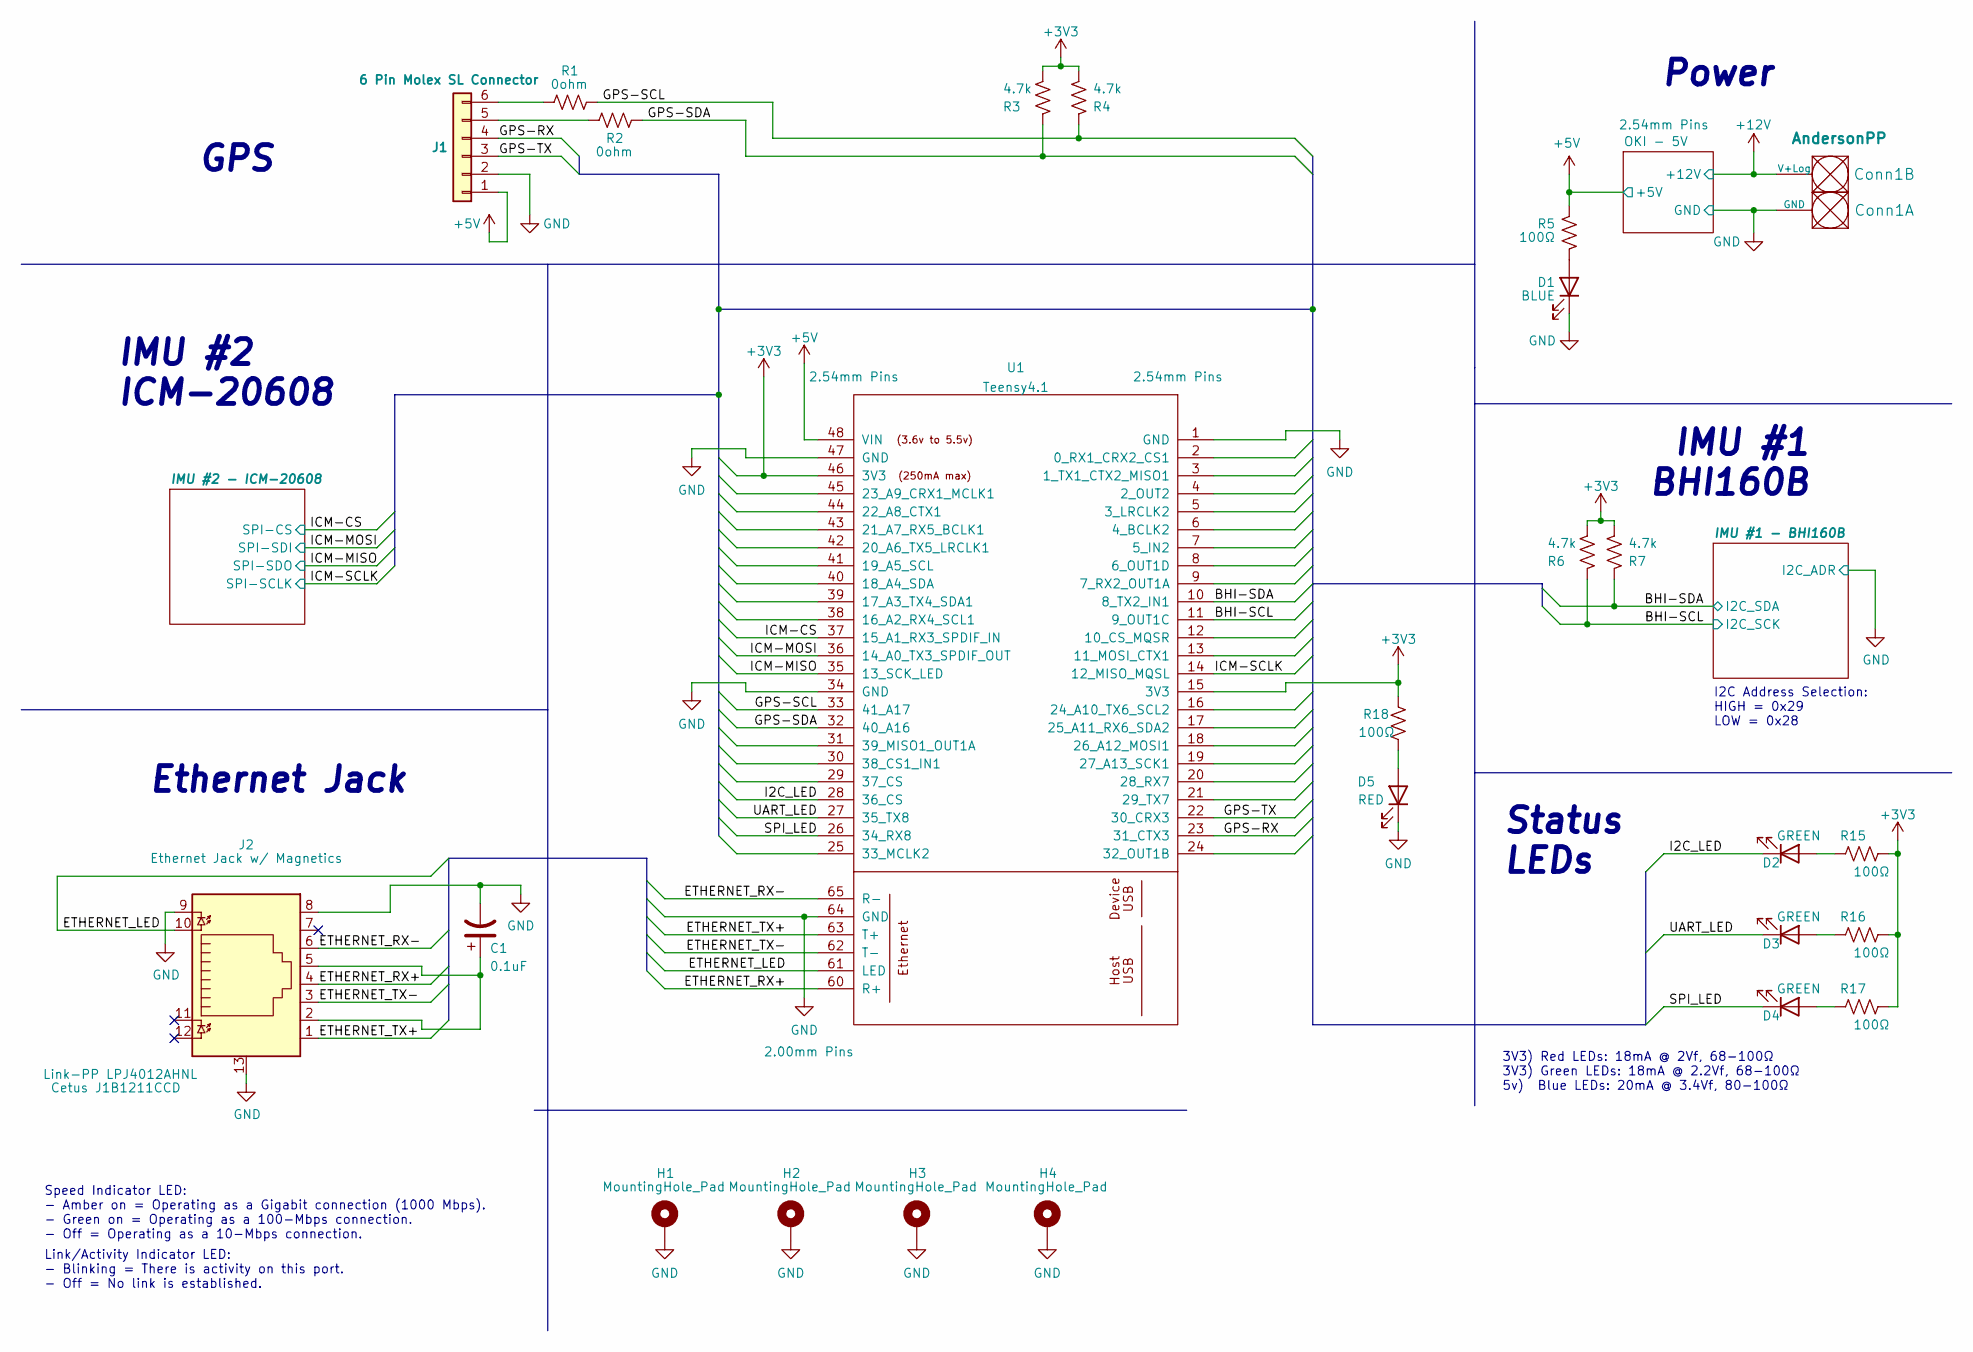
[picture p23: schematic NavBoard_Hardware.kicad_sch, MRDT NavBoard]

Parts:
C1: 0.1uF; C_0603_1608Metric_Pad1.08x0.95mm_HandSolder
Conn1: AndersonPP; Square_Anderson_2_H_Side_By_Side
D1: BLUE; LED_0603_1608Metric_Pad1.05x0.95mm_HandSolder
D2, D3, D4: GREEN; LED_0603_1608Metric_Pad1.05x0.95mm_HandSolder
D5: RED; LED_0603_1608Metric_Pad1.05x0.95mm_HandSolder
H1, H2, H3, H4: MountingHole_Pad
J1: 6 Pin Molex SL Connector; MOLEX_SL_06_Vertical
J2: Ethernet Jack w/ Magnetics; RJ45_Cetus_J1B1211CCD_Horizontal; Part Opt 1 Link-PP LPJ4012AHNL
R1, R2: 0ohm; R_0603_1608Metric_Pad0.98x0.95mm_HandSolder
R3, R4, R6, R7: 4.7k; R_0603_1608Metric_Pad0.98x0.95mm_HandSolder
R5, R15, R16, R17, R18: 100Ω; R_0603_1608Metric_Pad0.98x0.95mm_HandSolder
U1: Teensy4.1; Teensy41

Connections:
+5V: J1.1, R5.1, U1.48 (VIN); also elsewhere on the board
+12V: Conn1.2 (V+Log); also elsewhere on the board
/BHI-SCL: R6.1, U1.11 (9_OUT1C); also elsewhere on the board
/BHI-SDA: R7.1, U1.10 (8_TX2_IN1); also elsewhere on the board
/ETHERNET_LED: J2.10, U1.61 (LED)
/ETHERNET_RX+: J2.4, U1.60 (R+)
/ETHERNET_RX-: J2.6, U1.65 (R-)
/ETHERNET_TX+: J2.1, U1.63 (T+)
/ETHERNET_TX-: J2.3, U1.62 (T-)
/GPS-RX: J1.4, U1.23 (31_CTX3)
/GPS-SCL: R1.2, R4.1, U1.33 (41_A17)
/GPS-SDA: R2.2, R3.1, U1.32 (40_A16)
/GPS-TX: J1.3, U1.22 (30_CRX3)
/I2C_LED: D2.1 (K), U1.28 (36_CS)
/ICM-CS: U1.37 (15_A1_RX3_SPDIF_IN); also elsewhere on the board
/ICM-MISO: U1.35 (13_SCK_LED); also elsewhere on the board
/ICM-MOSI: U1.36 (14_A0_TX3_SPDIF_OUT); also elsewhere on the board
/ICM-SCLK: U1.14 (12_MISO_MQSL); also elsewhere on the board
/SPI_LED: D4.1 (K), U1.26 (34_RX8)
/UART_LED: D3.1 (K), U1.27 (35_TX8)
GND: C1.2, Conn1.1 (GND), D1.1 (K), D5.1 (K), H1.1, H2.1, H3.1, H4.1, J1.2, J2.8, J2.9, J2.13, U1.1 (GND), U1.34 (GND), U1.47 (GND), U1.64 (GND); also elsewhere on the board
unnamed: C1.1, J2.2, J2.5
unnamed: D1.2 (A), R5.2
unnamed: D2.2 (A), R15.2
unnamed: D3.2 (A), R16.2
unnamed: D4.2 (A), R17.2
unnamed: D5.2 (A), R18.2
unnamed: J1.5, R2.1
unnamed: J1.6, R1.1

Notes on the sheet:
Link/Activity Indicator LED: - Blinking = There is activity on this port. - Off = No link is established.
GPS
I2C Address Selection: HIGH = 0x29 LOW = 0x28
IMU #1 BHI160B
Status LEDs
IMU #2 ICM-20608
Speed Indicator LED: - Amber on = Operating as a Gigabit connection (1000 Mbps). - Green on = Operating as a 100-Mbps connection. - Off = Operating as a 10-Mbps connection.
Ethernet Jack
Power
3V3) Red LEDs: 18mA @ 2Vf, 68-100Ω 3V3) Green LEDs: 18mA @ 2.2Vf, 68-100Ω 5v) Blue LEDs: 20mA @ 3.4Vf, 80-100Ω

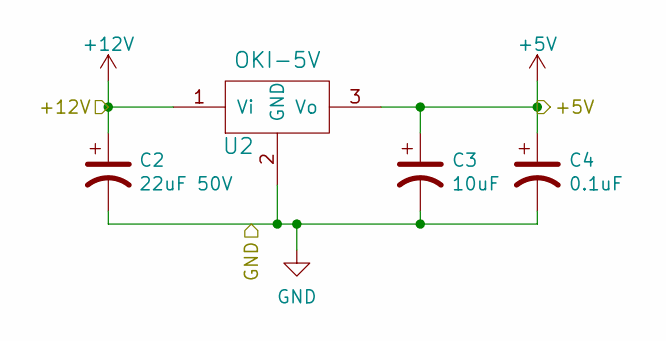
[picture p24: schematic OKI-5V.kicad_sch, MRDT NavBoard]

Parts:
C2: 22uF 50V; C_1206_3216Metric_Pad1.33x1.80mm_HandSolder
C3: 10uF; C_0603_1608Metric_Pad1.08x0.95mm_HandSolder
C4: 0.1uF; C_0603_1608Metric_Pad1.08x0.95mm_HandSolder
U2: OKI-5V; OKI_Vertical_TSR

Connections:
+5V: C3.1, C4.1, U2.3 (Vo); also elsewhere on the board
+12V: C2.1, U2.1 (Vi); also elsewhere on the board
GND: C2.2, C3.2, C4.2, U2.2 (GND); also elsewhere on the board

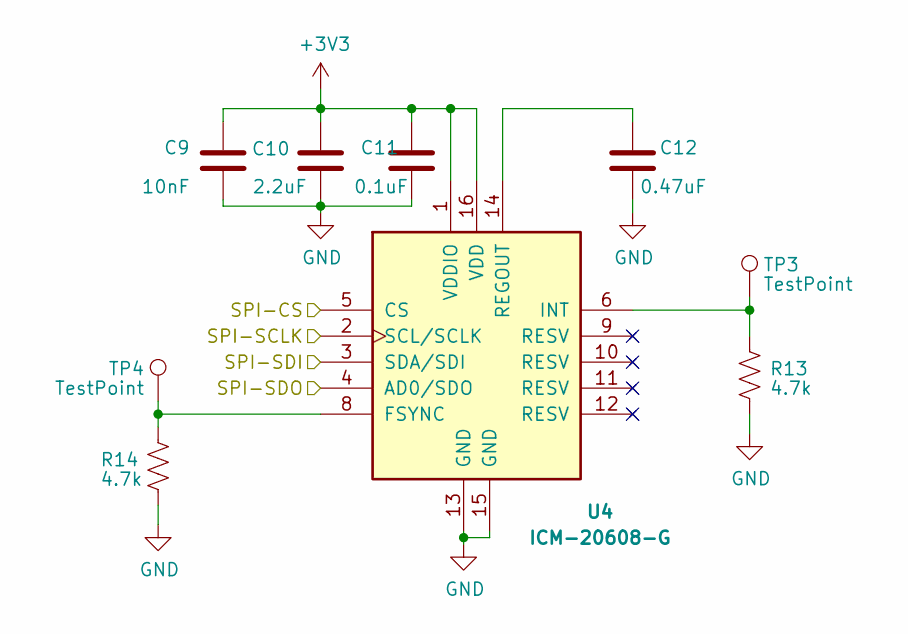
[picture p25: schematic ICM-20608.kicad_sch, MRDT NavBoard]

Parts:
C9: 10nF; C_0603_1608Metric_Pad1.08x0.95mm_HandSolder
C10: 2.2uF; C_0603_1608Metric_Pad1.08x0.95mm_HandSolder
C11: 0.1uF; C_0603_1608Metric_Pad1.08x0.95mm_HandSolder
C12: 0.47uF; C_0603_1608Metric_Pad1.08x0.95mm_HandSolder
R13, R14: 4.7k; R_0603_1608Metric_Pad0.98x0.95mm_HandSolder
TP3, TP4: TestPoint; TestPoint_Pad_D1.5mm
U4: ICM-20608-G; ICM-20608-G_ExtendedPads; PARTREV 1.0

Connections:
/ICM-CS: U4.5 (CS); also elsewhere on the board
/ICM-MISO: U4.4 (AD0/SDO); also elsewhere on the board
/ICM-MOSI: U4.3 (SDA/SDI); also elsewhere on the board
/ICM-SCLK: U4.2 (SCL/SCLK); also elsewhere on the board
GND: C9.2, C10.2, C11.2, C12.2, R13.2, R14.2, U4.13 (GND), U4.15 (GND); also elsewhere on the board
unnamed: C12.1, U4.14 (REGOUT)
unnamed: R13.1, TP3.1, U4.6 (INT)
unnamed: R14.1, TP4.1, U4.8 (FSYNC)

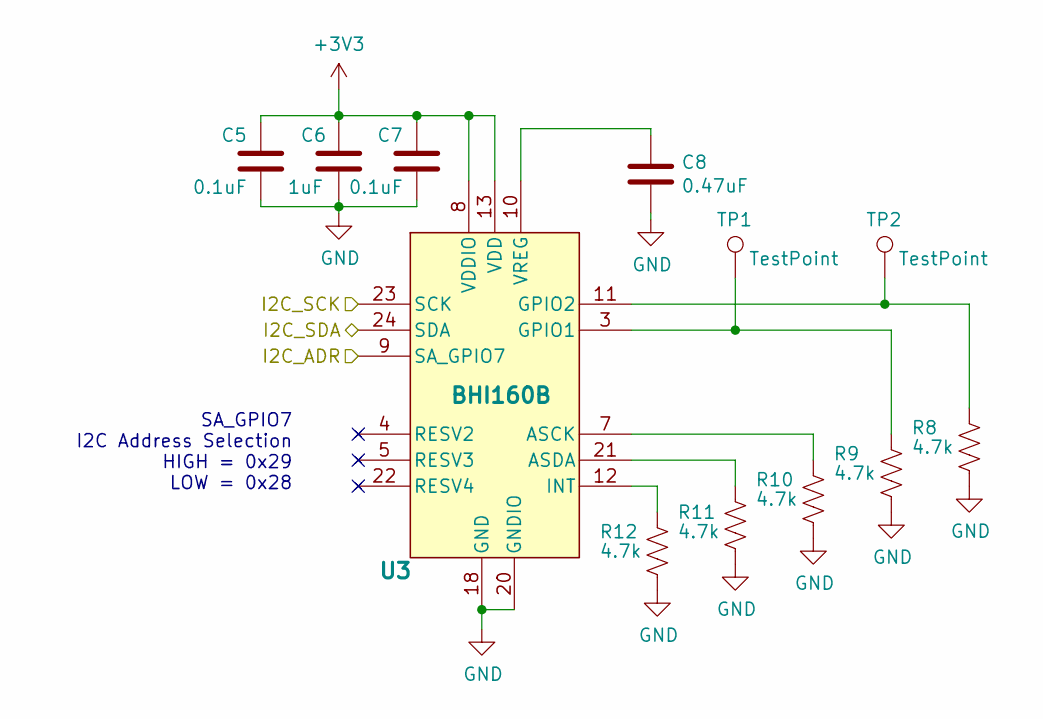
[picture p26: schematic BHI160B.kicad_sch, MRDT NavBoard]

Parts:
C5, C7: 0.1uF; C_0603_1608Metric_Pad1.08x0.95mm_HandSolder
C6: 1uF; C_0603_1608Metric_Pad1.08x0.95mm_HandSolder
C8: 0.47uF; C_0603_1608Metric_Pad1.08x0.95mm_HandSolder
R8, R9, R10, R11, R12: 4.7k; R_0603_1608Metric_Pad0.98x0.95mm_HandSolder
TP1, TP2: TestPoint; TestPoint_Pad_D1.5mm
U3: BHI160B; BHI160B_ExtendedPads

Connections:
/BHI-SCL: U3.23 (SCK); also elsewhere on the board
/BHI-SDA: U3.24 (SDA); also elsewhere on the board
GND: C5.2, C6.2, C7.2, C8.2, R8.2, R9.2, R10.2, R11.2, R12.2, U3.9 (SA_GPIO7), U3.18 (GND), U3.20 (GNDIO); also elsewhere on the board
unnamed: C8.1, U3.10 (VREG)
unnamed: R8.1, TP2.1, U3.11 (GPIO2)
unnamed: R9.1, TP1.1, U3.3 (GPIO1)
unnamed: R10.1, U3.7 (ASCK)
unnamed: R11.1, U3.21 (ASDA)
unnamed: R12.1, U3.12 (INT)

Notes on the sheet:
SA_GPIO7 I2C Address Selection HIGH = 0x29 LOW = 0x28

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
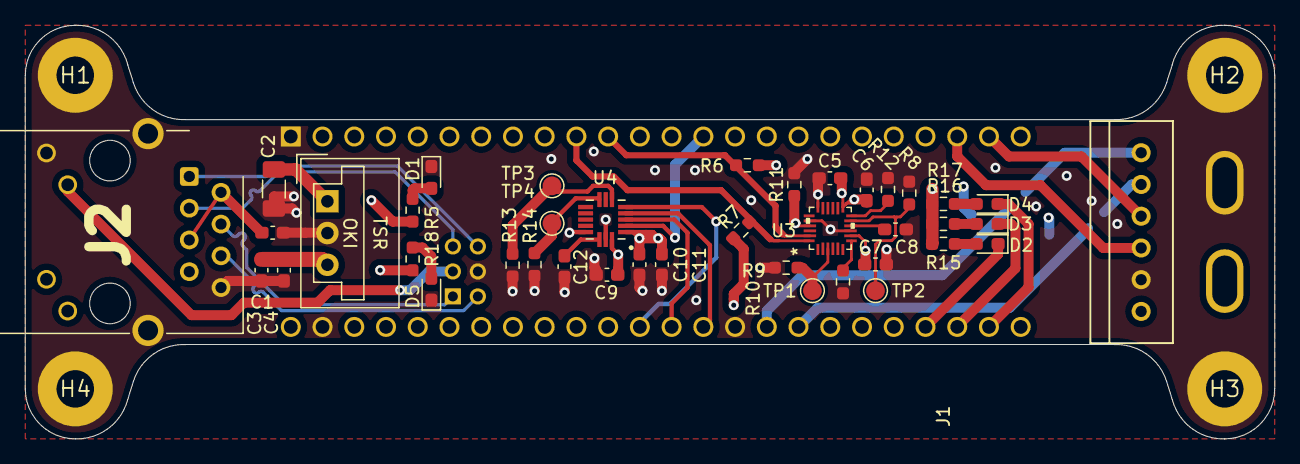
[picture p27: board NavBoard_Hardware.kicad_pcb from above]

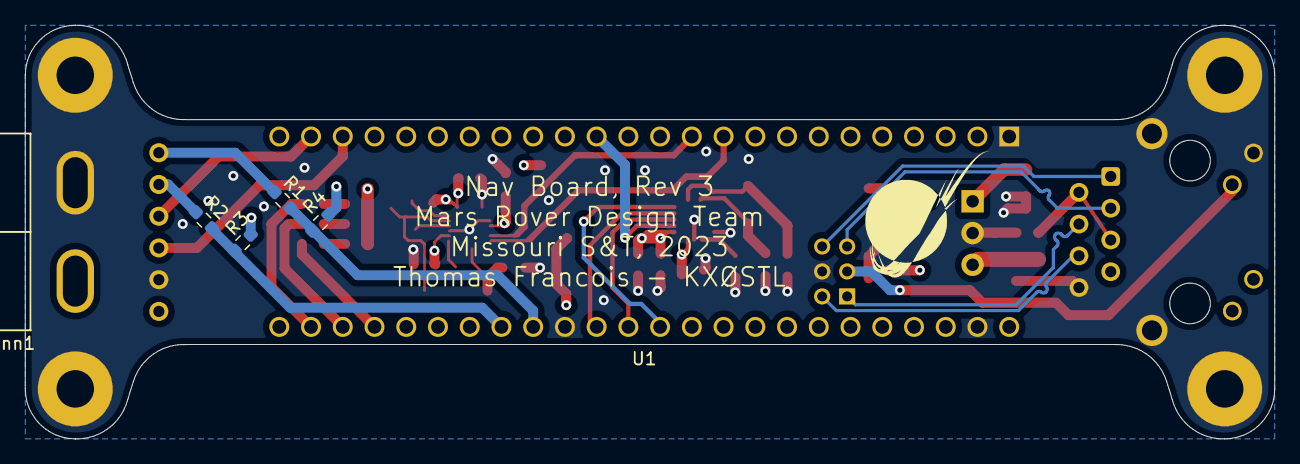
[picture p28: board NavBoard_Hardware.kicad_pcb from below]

Board: 4 copper layers, 100.0 x 33.1 mm, 50 parts (6 on the bottom side), 39 nets.

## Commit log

2015-10-05 Added GPS Schematic
    Added my version of the GPS thingy
    [Viehmann_GPS_2015.sch]
2015-10-05 Added GPS Schematic
    My version
    [Filla_GPS_2015.sch]
2015-10-19 Placed the distance between the headers
    [Viehmann_GPS_2015.brd]
2015-10-24 Finished first rev of the gps board
    Shout out to board space and Judah
    [Viehmann_GPS_2015.brd, Viehmann_GPS_2015.sch]
2015-10-26 Revision 1 of the GPS Board
    Super EAGLE Training
    [Filla_GPS_2015_Rev1.brd, Filla_GPS_2015_Rev1.sch]
2015-10-26 Created my first board!
    [Cruzada_GPS_2015_rev1.brd, Cruzada_GPS_2015_rev1.sch]
2015-10-26 Added bill of materials
    Here is the components to be put on the board
    [BOM.xlsx]
2015-10-26 Updated the folder structure
    Gave everyone there one folder
    [Cruzada_GPS_2015_rev1.brd, Cruzada_GPS_2015_rev1.sch, Filla_GPS_2015.sch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]
2015-10-26 Updated the git ignore and tested the files
    [Viehmann_GPS_2015.brd, Viehmann_GPS_2015.sch]
2015-10-31 Added all board files and things
    [BOM.xlsx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]
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2016-01-22 Added 3-Pin Connector
    Give this a look Judah and let me know if you need more stuffs
    [Viehmann_GPS_2015.brd, Viehmann_GPS_2015.sch]
2016-03-14 swapped power conn to app45 and put backup battery on top, gen'ed gerbers
    [Viehmann_GPS_2015.brd, Viehmann_GPS_2015.sch]
2016-10-13 Removed unnessasary files and file structure
    [Cruzada_GPS_2015_rev1.brd, Cruzada_GPS_2015_rev1.sch, Filla_GPS_2015.sch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]
2016-10-13 Renamed Board and Schematic files
    [NavigationBoard.brd, NavigationBoard.sch]
2016-10-13 Deleted Bill of Materials
    [BOM.xlsx]
2016-11-05 Added new NavBoard file, Removed old Navigation Board files
    [NavBoard.sch, NavigationBoard.brd, NavigationBoard.sch]
2016-11-05 Added LSM9DS1 IMU to circuit
    Wired up the IMU breakout board to Tiva and changed RX and TX notation
    tags to RX(2) and TX(2).
    [NavBoard.sch]
2016-11-05 Completed first version of PCB design and added power connectors and regulator to schematic and board
    Completed first version of board design, added 12v anderson connectors
    to schematic along with 5v regulator and 10 uF capacitors, and changed
    RX(2) and TX(2) to RX(6) and TX(6).
    [NavBoard.brd, NavBoard.sch]
2016-11-07 Finished revision 1 of board design
    Schematic: Connected INTM, INT1, INT2, and DRDYM from IMU to pins PL0
    through PL3 on the Tiva. Added two new capacitors to power input of the
    GPS chip. Added a capacitor to the battery power supply.
    Board: Added top layer ground plane with ground plane stitching, added
    mounting holes for the navigation board, arranged all component names on
    board so they would be visible once they were silk screened, and added
    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
    [NavBoard.brd, NavBoard.sch]
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2018-10-14 Finalized high lvl schematic
    [2019NavBoard.kicad_pcb, 2019NavBoard.sch]
2018-10-16 Fixed cut lines on PCB layout
    [2019NavBoard.kicad_pcb]
2018-10-20 Fixed Errors and added a LIDAR
    Some of the gobal labels had to be fixed and I added a LIDAR to the schematic. Also added some .txt files for pdr.
    [2019NavBoard.kicad_pcb, 2019NavBoard.sch]
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2018-11-04 Slight changes to PCB traces
    [2019NavBoard.kicad_pcb]
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2018-11-15 Edit traces before review
    [2019NavBoard.kicad_pcb]
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2018-11-18 Deleted old files, renamed files to NavBoard Hardware
    [2019NavBoard.sch, NavBoard_Hardware.kicad_pcb]
2018-12-01 fixed file errors
    [2019NavBoard.kicad_pcb, 2019NavBoard.sch]
2018-12-01 revised schematic after meeting
    [2019NavBoard.sch]
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2018-12-10 Editied schematic and made PCB
    [2019NavBoard.kicad_pcb, 2019NavBoard.sch]
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2018-12-15 Fixed traces
    [2019NavBoard.kicad_pcb, 2019NavBoard.sch]
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2018-12-16 BOM and other files for review
    [NavBoard_Hardware.kicad_pcb, NavBoard_Hardware.sch, NavBoard_Hardware_BOM.csv]
2018-12-16 just in case push
    [NavBoard_Hardware-B.Cu.gbr, NavBoard_Hardware-B.Mask.gbr, NavBoard_Hardware-B.Paste.gbr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]
2019-02-15 Updated to rev2 libraries
    [NavBoard_Hardware.kicad_pcb, NavBoard_Hardware.sch]
2019-02-15 updated rev 2 libraries
    [NavBoard_Hardware.sch]
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2019-03-02 Finsihed all changes by Andrew Starting PCB
    [NavBoard_Hardware.kicad_pcb, NavBoard_Hardware.sch]
2019-03-02 Traces and PCB begin
    [NavBoard_Hardware.kicad_pcb]
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2019-03-03 Added level shifter to board and made traces beautiful
    I, Andre did alot. I sleep now
    [NavBoard_Hardware.kicad_pcb, NavBoard_Hardware.sch]
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2019-03-04 fixed direction of signs
    [NavBoard_Hardware.sch, _saved_NavBoard_Hardware.sch]
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2019-03-05 Fixed DRC Polygons
    [NavBoard_Hardware.kicad_pcb]
2021-10-09 Duplicated last year's board with a few changes
    BMX160 was replaced with BNO080 and LiDAR circuit was removed. Reorganized schematic and cleaned up some wires.
    [NavBoard_Hardware.csv, NavBoard_Hardware.kicad_pcb, NavBoard_Hardware.sch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]
2021-10-15 Finished wiring BNO080 circuit
    Also changed values of indicator resistors
    [NavBoard_Hardware.sch]
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2021-10-24 Added backup battery for GPS
    Change was discussed in PDR. Also fixed input to BNO080.
    [NavBoard_Hardware.sch]
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2021-11-19 CDR Changes 2
    Ready to release, signatures to be added
    [NavBoard_Hardware-B_Cu.gbr, NavBoard_Hardware-B_Mask.gbr, NavBoard_Hardware-B_Paste.gbr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]
2021-11-21 Signature
    Added my signature on the board. Still needs one more.
    [NavBoard_Hardware.kicad_pcb]
2021-11-21 Fixed Signature
    [NavBoard_Hardware.kicad_pcb]
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2021-12-30 removed rescue libraries & fixed symbol associations. imported IMU footprints to MRDT_KICAD_LIBRARIES
    [NavBoard_Hardware.sch]
2022-09-07 Initial pass at stackable arrangement
    Attempting to replace previous board design with 2 daughter boards, using a Teensy 4.1 instead of a Raspberry Pi
    [NavBoard_Hardware.kicad_pcb, NavBoard_Hardware.kicad_sch]
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2022-09-18 Redesigned layoput
    [NavBoard_Hardware.kicad_pcb, main_board.kicad_sch, teensy-shield.kicad_sch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]
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2022-10-07 Fixed pinout of 24pin-to-16pin adapter footprint
2022-10-07 Corrected pinout of RJ45 symbol, squashed some bugs
    [NavBoard_Hardware.kicad_sch, main_board.kicad_sch, teensy-shield.kicad_sch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]
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2022-10-09 Added 3D models for pin sockets and headers
    [NavBoard_Hardware.kicad_pcb]
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2022-10-09 Generated 3D renderings, animation, and schematic review PowerPoint
    [NavBoard_Hardware.kicad_pcb]
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2022-11-01 Rearranged schematic
    I realize now that this is a dumb idea...
    Going to redesign the board so the teensy just sits on top
    [NavBoard_Hardware.kicad_pcb, NavBoard_Hardware.kicad_sch, OKI-5V.kicad_sch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]
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2022-11-03 Realized this could all fit on a single board
    [BHI160B.kicad_sch, ICM-20608.kicad_sch, NavBoard_Hardware.kicad_sch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]
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2022-11-25 Updated repo with up-to-date schematic and pcb
    Not sure why this happened, but the repo should be up to date now. We should try to cancel the PCB order and reupload this board if that's still possible.
    [NavBoard_Hardware-B_Mask.gbs, NavBoard_Hardware-B_Paste.gbp, NavBoard_Hardware-B_Silkscreen.gbo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]
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

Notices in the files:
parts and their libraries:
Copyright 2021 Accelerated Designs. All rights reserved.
